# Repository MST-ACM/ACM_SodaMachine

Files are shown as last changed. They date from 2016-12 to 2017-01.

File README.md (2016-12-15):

# ACM Soda Machine Documentation
This documentation details all of information necessary to start, develop, maintain, and update the Soda Machine in CS 213.

## Dependencies
1. [Pyserial](https://github.com/pyserial/pyserial)
  + ```Pyserial``` handles the serial communication of authorization and logging characters between the Raspberry Pi and Arduino platforms in the soda machine.
2. [Pymysql](https://github.com/PyMySQL/PyMySQL)
  + ```Pymsql``` handles the connection to the SQL-lite database stored locally on the Raspberry Pi machine which stores the currency (i.e. how much money each user has).
3. [Libusb1](https://github.com/vpelletier/python-libusb1)
  + ```Libusb1``` handles the interfacing between the LCD screen and the Raspberry Pi so that the Raspberry Pi can write messages to the LCD.
4. [Evdev](https://python-evdev.readthedocs.io/en/latest/)
  + ```Evdev``` handles Kernel input interfacing for the magnetic strip reader when a user swipes their card.
5. [Nanpy](https://github.com/nanpy/nanpy)
  + ```Nanpy``` handles the direct throughput and communication to the arduino board through python.

## Installation
When migrating or reinstalling the system, please follow the following commands on the Raspberry Pi shell to install the main soda machine files ```NOT DEPENDENCIES```:
```
mkdir ~/pi/Soda-Machine/
cd ~/pi/Soda-Machine/
git init
git clone https://github.com/MST-ACM/ACM_SodaMachine_2.0.git
chmod +x main.py bin/smadmin bin/smdaemon
mv Documentation/sodamachine.init /etc/init.d/sodamachine
sudo update-rc.d sodamachine defaults
sudo service sodamachine restart
```
## Pseudocode Overview
1. The user swipes their Student ID into the magnetic strip reader which the magnetic strip reader translates to a ```Student ID```
2. ```Main.py``` performs a database lookup on the Student ID to determine if the user has the required funds.
3. If the database lookup is successful, the Raspberry Pi sends an authorization character to the Arduino using the serial connection.
  - If the database lookup is not successful the transaction fails and the Raspberry Pi resets it transaction state.
4. After the Arduino receives the authorization character, it waits for the user to press a button on the soda machine
  - If the user does not press a button after a certain amount of seconds, the transaction fails and the Raspberry Pi and Arduino reset their states.
5. After the user presses a button, the Arduino turns on the motor associated with the button until the soda is dispensed.
6. After the soda is dispensed, the Arduino sends a success character back to the Raspberry Pi so that the Raspberry Pi charges the user for the soda
  - The user is charged here instead of step 4 to prevent any errors with a soda failing to be dispensed.
7. Then, the Arduino and Raspberry Pi reset their states for the next transaction.

## Contribute
Please contact [acm@mst.edu](acm@mst.edu) if you would like to contribute to this project.

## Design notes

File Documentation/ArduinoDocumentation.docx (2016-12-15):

Arduino Mega code is a slightly modified C code. A reference page can be found at the following website, showing Arduino specific functions and their uses: http://arduino.cc/en/Reference/HomePage. The Arduino Mega code is is broken into two main pieces. The first peice of code is simply initialization of the Arduino Mega and the pins it will be accessing. It also runs through each of the motors and rotates them to a proper starting position and checks the stock to set empty as appropriate.

The second bit of code is the main loop. This loop will just continually cycle while the machine is running. The loop itself is broken into two sub-loops.

The first sub-loop waits for proper authorization to be given by the Raspberry Pi. Presumably a card swipe will be used by the Raspberry Pi to give authorization, though any authorization methods would work. All authorization checks should be done here. Currently, the code automatically authorizes a user. This is for testing purposes only.

The second sub-loop continuously cycles a for-loop waiting for button-press input corresponding to a still stocked soda. At this point the controller will power a motor, have it remained powered until it completes its cycle appropriately then end powering a motor while revoking purchasing permission. Currently, the code does not revoke permission, simply leaving it as “true”. If soda stock is low, the The sub-loop will end and return to the first sub-loop, waiting for authorization again.

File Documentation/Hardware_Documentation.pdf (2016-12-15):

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

ACM Soda Machine

## Introduction

In this document, the reader will nd information on the theory of operation and design of the ACM Soda Machine. Aspects of the soda machine that will be discussed in detail include the controller and the overall wiring of the machine. After reading this document, the reader will have an understanding of how the controller interfaces with machine components such as buttons and motors.

## Overview

A block diagram representation of the overall system can be seen in Figure 1.

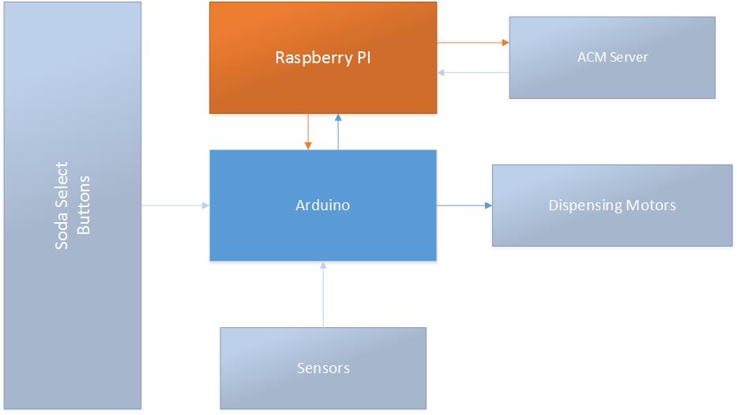
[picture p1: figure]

Figure 1: System Block Diagram

The controller is represented by the block labeled Arduino. The controller implements an Arduino Mega 2560 to read inputs as well as to control the motors. Furthermore, it communicates with the Raspberry Pi in order to receive authorization as well as to relay information concerning soda stock. This document will begin by explaining the theory behind motor operation and control, continue to discuss the inventory sensors and soda select buttons, and conclude with a discussion of the controller itself. The discussion on motor operation and soda select buttons must be read with the Arduino environment in mind; in particular, it is recommend that the reader be familiar with the basics of the Arduino (in particular, the important concept is the idea of using digital pins to read inputs as well as to control outputs).
The overall process of dispensing a soda in terms of conrmations, error checking, and general protocol (conrming payment, receiving authorization from the Raspberry Pi, waiting for a button press. . . ) will not be discussed in this document; rather, the operation of each sub-system will be discussed from a hardware perspective.
Throughout this document, signals may be referred to by their signal names; these names correspond to the names that are used in the Eagle Cad design les for the controller.

Hardware Documentation - Page 2 of 13

## Motor Operation

The soda machine has eight motors (Figure 2), each with identical modes of operation. All eight motors require 120 V AC in order to turn on; when a give motor is running, it will draw 1.15 A. Any design modication must take these parameters into consideration. Because of the way that the software is written, it should not be possible for more than one motor to be active at a given time.

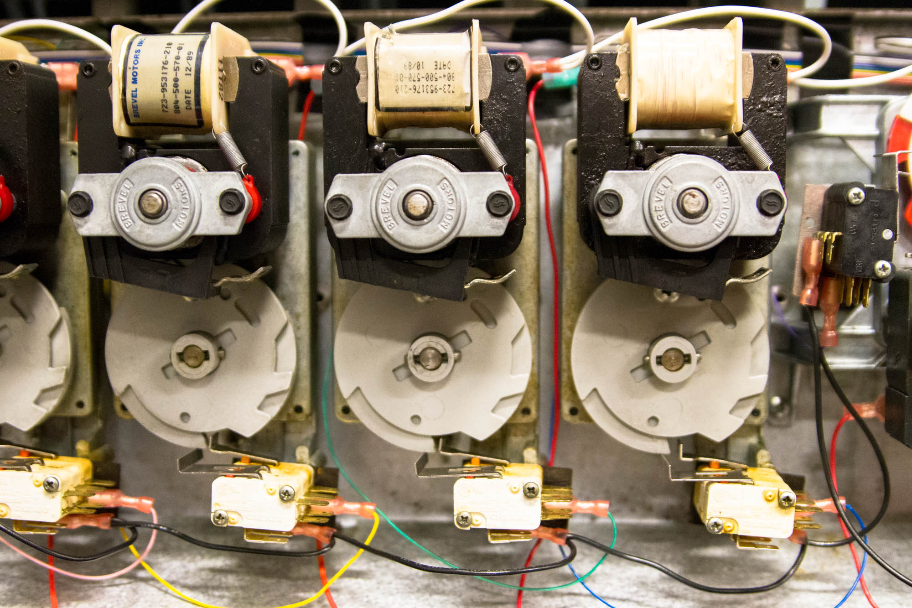
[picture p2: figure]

Figure 2: Machine Motors

The red wires that connect to the left end of the coil windings are connected to the controller; when a motor is to be activated, it is through the red wire that the controller will supply the 120 V AC. All of the motors are tethered to each other via the white wire. The white wire connects directly to the controller, where it is then connected to the neutral line of the 120 V AC power from the socket.
The motor control works by implementing the rotational disks and the switches that are on the motors (Figure 3).

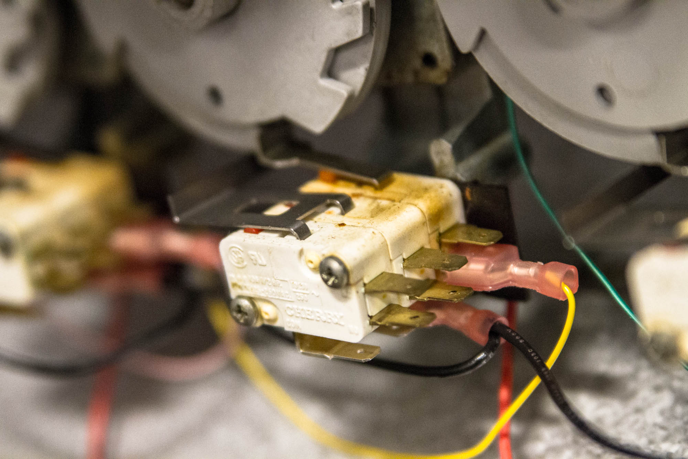
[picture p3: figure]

Figure 3: Motor Control Switch

When a soda is to be dispensed, 120 V AC must be supplied to the appropriate motor for a period of time that is long enough to allow the disk to make a full revolution. In order to achieve the appropriate amount of time, the controller monitors the state of the switch as the motor rotates. When a motor is initially turned on, the controller waits for a short period of time (just enough time for the disk to rotate to a degree where the disk closes the switch) and then it begins monitoring the state of the switch; once the disk makes a full revolution, and when the switch snaps back open, the controller ceases to supply power to the motor.
The black wires that connect each of the switches together are signal ground of the controller. The colored ribbon cable wire of each switch connects to a specic pin on the Arduino through the controller; the pins are held HIGH via internal pull-up resistors in the Arduino. When a motor is mid-rotation and the switch is closed, the ribbon cable wire will short to ground and the controller will supply power for as long as it reads a signal ground from the switch.
The motor numbering convention is 1-8, going from left right, facing the machine. A summary of the wire colors and signal names for the motor system is given in Table 1; a summary of the control signal (ribbon cable wires) mapping to the Arduino's digital pins is given in Table 2. Details concerning the method by which power is supplied to the motors will be provided in the section on the controller itself.
Motor Sub-system | Wire Color | Signal Name
Power | Red | MOTOR1. . . MOTOR8
Power | White | NEUTRAL
Control | Assorted (Ribbon Cable) | CYCLE_SENSE1. . . CYCLE_SENSE8
Control | Black | GND

Table 1: Motor System Wiring

Signal Name | Arduino Pin Number
CYCLE_SENSE1 | 41
CYCLE_SENSE2 | 40
CYCLE_SENSE3 | 39
CYCLE_SENSE4 | 38
CYCLE_SENSE5 | 37
CYCLE_SENSE6 | 36
CYCLE_SENSE7 | 35
CYCLE_SENSE8 | 34

Table 2: Control Signal Pin-mapping

## Inventory Sensors

As the soda cans sit in their slots, they press down on one side of a lever, causing the opposite side to elevate; the opposite side of the lever is the side that presses (or depresses when there is no soda) a mechanical switch. These mechanical switches are the inventory sensors (Figure 4).
Each sensor has two sets of switches that are adjacent to each other: Orienting the switch such that the metal tabs are facing you, the set of tabs on the right-hand side correspond to the inventory stock; the ribbon cable connected to the right-hand side switch connects to pins on the Arduino through the controller.
The inventory switches essentially operate the same way that the motor control switches operate: One end of each inventory switch is connected to the controller's ground and the other end of the switch is connected to a specic pin on the Arduino; the Arduino pin is held HIGH with an internal pull-up resistor and, when a particular soda runs out, the switch is closed and the signal shorts to ground.

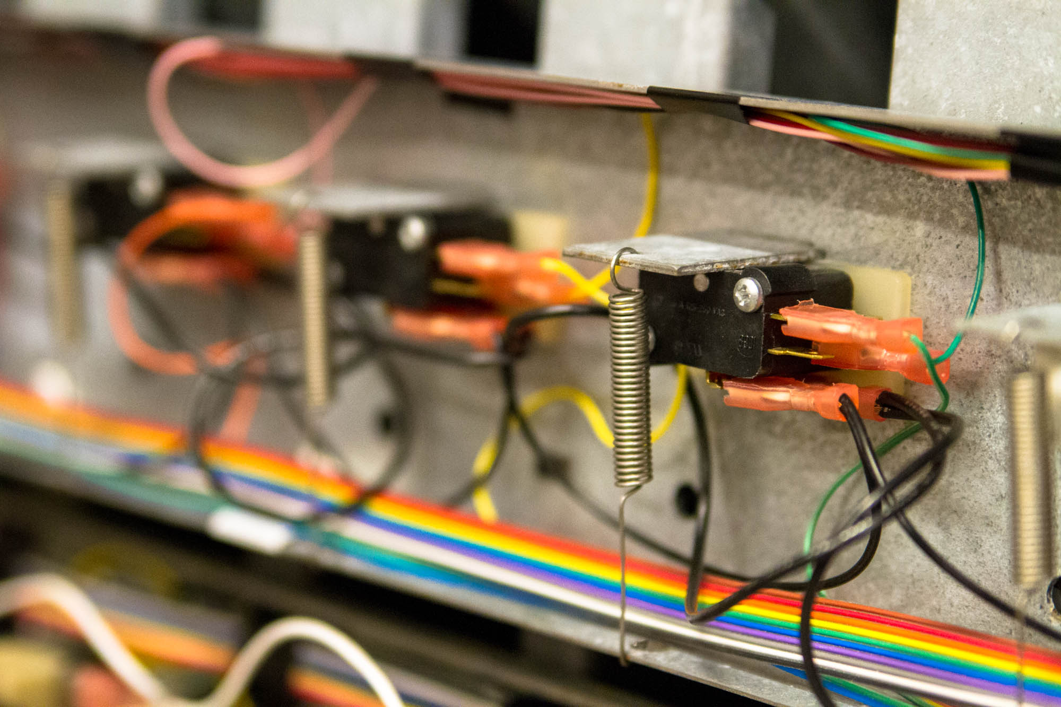
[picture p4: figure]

Figure 4: Inventory Sensors

The Arduino pins used for the stock sensors are analogue pins, as opposed to digital pins (for the purposes of this project, there is little bearing on whether a pin is digital or analogue). The numbering convention of the inventory sensors is identical the motor numbering convention: From left to right, they are 1-8. Table 3 summarizes the inventory signals and their corresponding Arduino pin numbers.

Signal Name | Arduino Pin Number
SENSOR1 | A0
SENSOR2 | A1
SENSOR3 | A2
SENSOR4 | A3
SENSOR5 | A4
SENSOR6 | A5
SENSOR7 | A6
SENSOR8 | A7

Table 3: Inventory Sensor Pin-mapping

The set of tabs on the left-hand side of the inventory switch corresponds to the LEDs of the buttons; these signals do not correspond to any pins on the Arduino. Each LED switch has one end connected to the controller's +5 V pin and the other end of the switch is connected to a particular LED's anode; the cathode of each LED is connected to the controller's ground. When a soda is in stock, the LED will be supplied with power; however, when a particular soda runs out and the lever presses down on the switch, the LED will be disconnected from the power supply and the LED will turn o.

NOTE: At it its current state, there is a set of wires, one green (which connects to ground) and one blue (which connects to +5 V ), running from the LED switches to the controller. At the controller end, the wires have pins on their ends, but they are not plugged into the connector that would mate with the +5 V /GND headers on the controller. DO NOT neglect obtaining the proper connector before connecting the wires to the board; if you do, you risk shorting the +5 V pin on the Arduino with the GND pin, which could cause the Arduino to fry if it goes unnoticed. The appropriate connector that is needed for this is a Molex connector (MFG Part#: 22-01-2025). It might be possible to obtain free samples of this connector directly from Molex; if not, they are available on Mouser.

## Soda Select Buttons

The soda select buttons (Figure 5) essentially operate the same way that the motor control and inventory switches operate: One end of each button is connected to the controller's ground and the other end of the button is connected to a specic pin on the Arduino; the Arduino pin is held HIGH with an internal pull-up resistor and, when a button is pressed, the Arduino recognizes the short to ground.

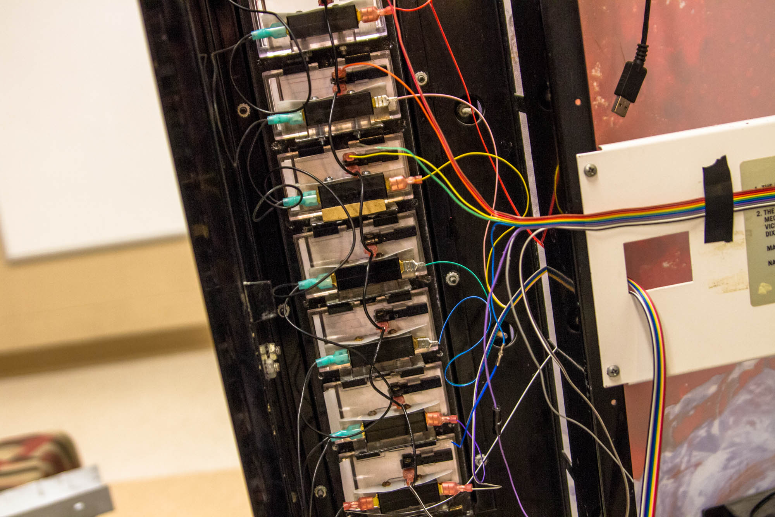
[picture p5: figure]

Figure 5: Soda Select Buttons

The ribbon cable labeled as Buttons is the one that corresponds to the Arduino pins involved with monitoring the button select system; the Arduino pins used for the buttons are analogue pins, as opposed to digital pins. The button numbering convention is 1-8, going from top to bottom. Table 4 summarizes the button signals and their corresponding Arduino pin numbers.

Signal Name | Arduino Pin Number
BUTTON1 | A8
BUTTON2 | A9
BUTTON3 | A10
BUTTON4 | A11
BUTTON5 | A12
BUTTON6 | A13
BUTTON7 | A14
BUTTON8 | A15

Table 4: Soda Select Button Pin-mapping

## The Controller

The controller can be seen in Figure 6.

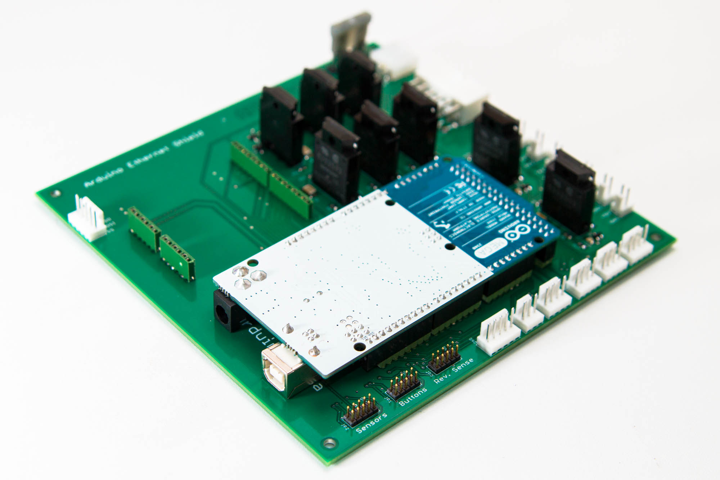
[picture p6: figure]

Figure 6: The Controller

Power Connector

The power connector can be seen in Figure 7.

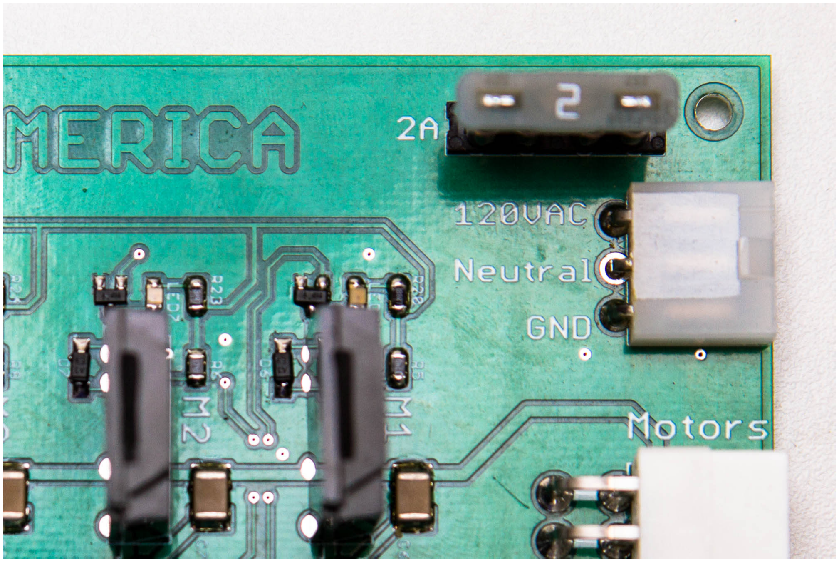
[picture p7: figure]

Figure 7: Power Connector

The Neutral line goes immediately to a pin on the adjacent Motors connector, from where it goes to the motors. At its current state, the GND line goes directly to a pin on the Motors connector, but to nowhere else; in the future, a wire could be run from this GND pin and connect to the machine chassis via a round terminal. The 120 V AC line is distributed to one of the output pins of each motor relay (Figure has the 120 V AC signal highlighted).

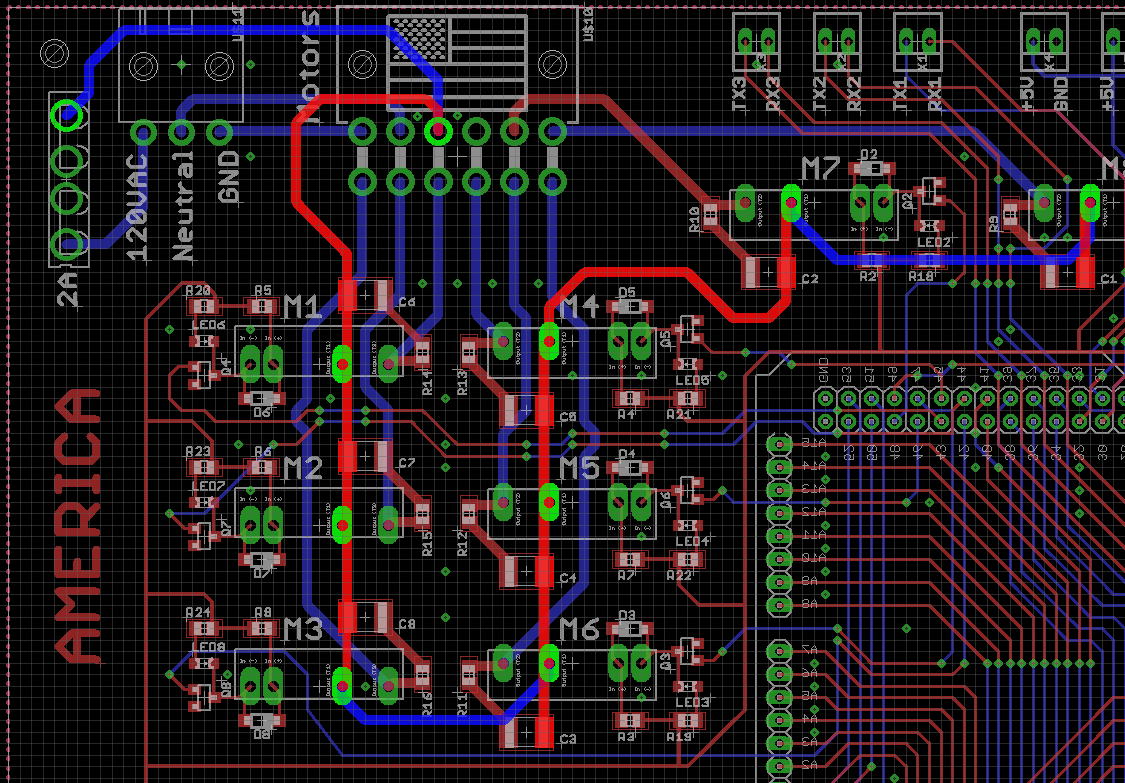
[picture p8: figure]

Figure 8: 120 V AC Highlighted

However, before the 120 V AC line is distributed, it goes through a fuse; the fuse protects the board from current surges. The 120 V AC traces have widths of 40 mils; using a copper thickness of 1 oz/f t² ,
the current carrying capability of the traces is about 2.4 A. The fuse must be able to carry more than 1.15 A, but MUST NOT BE ABLE TO CARRY MORE THAN 2.4 A. A 2.0 A fuse is recommended. The fuse holder takes ATC blade fuses.
The second output pin of each relay is connected to a pin on the Motors connector; these pins are what connect to the motors through the red wires.

Motors Connector

The numbering convention for the pins on the Motors connector follows what is indicated in Figure 9. Table 5 gives the signal names corresponding to the pins on the Motors connector.

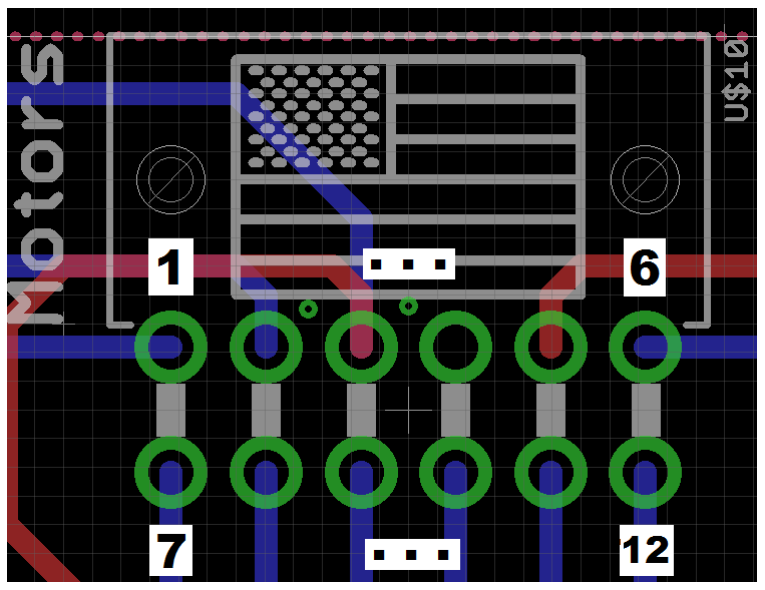
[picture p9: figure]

Figure 9: Motor Connector Numbering

Connector Pin Number | Signal Name
1 | 120VAC-GND
2 | NEUTRAL
3 | 120VAC
4 | NC
5 | MOTOR7
6 | MOTOR8
7 | MOTOR3
8 | MOTOR2
9 | MOTOR1
10 | MOTOR4
11 | MOTOR5
12 | MOTOR6

Table 5: Motors Connector Pin-out

Relay Circuitry

The relays that are used to interface between the Arduino and the motors are solid state relays made by Sharp Microelectronics (MFG Part #: S202S01F). Between the input and output sides, the relays provide 4.0 kV of isolation and they are rated for 8.0 A. The relay circuitry for a single motor is shown in Figure 10.

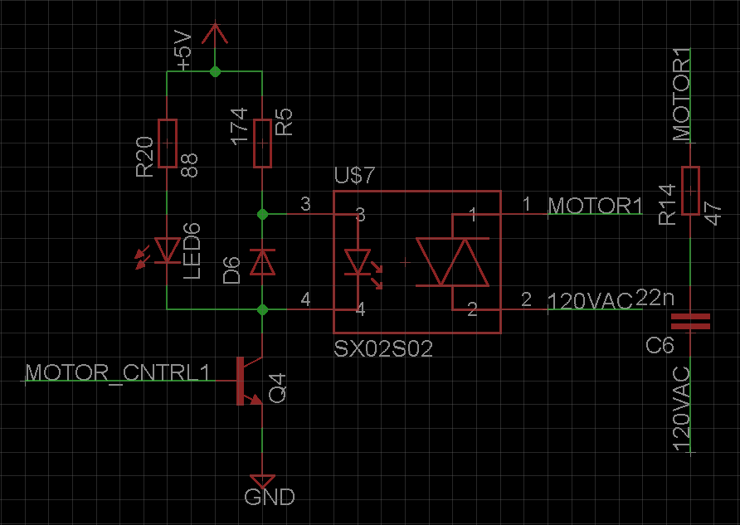
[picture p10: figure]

Figure 10: Relay Circuitry

Essentially, in order to turn a motor on, the internal LED of the relay needs to be turned on. This is accomplished by rst supplying +5 V to the anode pin of the relay while also using a current-limiting resistor to protect the internal LED. The signal, MOTOR_CNTRL1, connects to a digital pin on the Arduino. When this signal goes HIGH, the transistor turns on, completing the input circuit of the relay and allowing current to ow through the relay LED. When this happens, MOTOR1 (which connects to the rst motor through the Motors connector) is connected to the 120 V AC line, turning the motor on. The motor control signal (in this case, MOTOR_CNTRL1) remains HIGH until the motor makes a full revolution; that is, it remains HIGH until the Arduino ceases to read a LOW state from the motor control signal (in this case, the rst motor would remain on until CYCLE_SENSE1 stopped registering as LOW). When a motor is to be turned o, the motor control signal is set to LOW, essentially creating an open-circuit condition in the relay's input circuit.
Table 6 summarizes the motor control signals and their corresponding Arduino pin numbers.
Signal Name | Arduino Pin Number
MOTOR_CNTRL1 | 44
MOTOR_CNTRL2 | 43
MOTOR_CNTRL3 | 42
MOTOR_CNTRL4 | 45
MOTOR_CNTRL5 | 46
MOTOR_CNTRL6 | 47
MOTOR_CNTRL7 | 48
MOTOR_CNTRL8 | 49

Table 6: Motor Control Pin-mapping

Communication and Auxiliary Pins

The controller has easy access to the Arduino's communication pins; the communication pins are summarized in Table 7.

Signal Name | Arduino Pin Number
MISO | 50
MOSI | 51
SCK | 52
SS | 53
TX3 | 14
RX3 | 15
TX2 | 16
RX2 | 17
TX1 | 18
RX1 | 19

Table 7: Communication Pin-mapping

Furthermore, the controller has six auxiliary ports that provide easy access to all other unused Arduino pins. Table 8 gives the Arduino pin numbers corresponding to each auxiliary pin.

Auxiliary Port 1

Signal Name | Pin Number
AUX1.1 | 31
AUX1.2 | 32
AUX1.3 | 33

Auxiliary Port 2

Signal Name | Pin Number
AUX2.1 | 28
AUX2.2 | 29
AUX2.3 | 30

Auxiliary Port 3

Signal Name | Pin Number
AUX3.1 | 25
AUX3.2 | 26
AUX3.3 | 27

Auxiliary Port 4

Signal Name | Pin Number
AUX4.1 | 22
AUX4.2 | 23
AUX4.3 | 24 | AUX6.3 | 12
| | AUX6.4 | 13

Auxiliary Port 5

Signal Name | Pin Number
AUX5.1 | 21
AUX5.2 | 20

Auxiliary Port 6

Signal Name | Pin Number
AUX6.1 | 10
AUX6.2 | 11

Table 8: Pin-mapping for Auxiliary Ports

Establishing Communication With the Raspberry Pi

Perhaps the simplest way to establish communication between the Raspberry Pi and the Arduino would be to take advantage of the Arduino's I

2C pins, which can easily be accessed with auxiliary

pins AUX5.1 (SCL) and AUX5.2 (SDA).

NOTE: DO NOT use this method unless the Raspberry Pi is being run as a master and the Arduino is being run as a slave. If the situation is otherwise, you will need to use a dierent method that incorporates a logic level converter to interface between the Raspberry Pi and the Arduino.

The header which has AUX5.1 and AUX5.2 is a three-pin header which also includes GND. In order to connect with the Raspberry Pi, simply connect the Arduino's GND to the Raspberry Pi's GND, AUX5.1 with the Pi's SCL pin, and AUX5.2 with the Pi's SDA pin.

For cable assembly: The wires on the Arduino end of the cable will need to be tted with crimp terminals (Molex Part #: 39-00-0039) which will be fed into a mating connector (Molex Part #: 22-01-2035). Be sure to orient the wires into the connector correctly so that the pins on the Arduino connect to the correct pins on the Raspberry Pi.

Further details can be found here: http://blog.oscarliang.net/raspberry-pi-arduino-connected-i2c/.

## Final Notes

During the nal testing of the controller, it was noticed that if the machine is turned o and then turned back on too quickly, there is a possibility of blowing the fuse. For this reason, it is recommended that, when the machine is turned o, it be given a chance to cool down for about 10 seconds before turning it back on.
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

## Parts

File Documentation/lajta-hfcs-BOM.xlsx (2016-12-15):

Board Name: | lajta-hfcs | Quantity: | 2
Description: | Controller for ACM soda machine.
Board Vrsn: | 1V1 | Client: | ACM
Date: | 2014-05-14
Item # | Qty | Totals | Ref Des | Value | Manufacturer | Mfg Part # | Digikey Part # | Mouser Part # | Description | Package | Alt Mfg Part #s
PCB Assembly
1 | 8 | 16 | C1, C2, C3, C4, C5, C6, C7, C8 | 22n | Murata | GA243QR7E2223MW01L |  | 81-GA243QR7E2223MW1L (http://www.mouser.com/ProductDetail/Murata-Electronics/GA243QR7E2223MW01L/) | Multilayer Ceramic Capacitors MLCC - SMD/SMT .022uF 250Volts 20% | C1812
2 | 8 | 16 | D1, D2, D3, D4, D5, D6, D7, D8 | 1N4448W | Vishay | 1N4448W-E3-08 |  | 78-1N4448W-E3-08 (http://www.mouser.com/ProductDetail/Vishay-Semiconductors/1N4448W-E3-08/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) | Diodes - General Purpose, Power, Switching 100 Volt 500mA 4ns | SOD123
3 | 1 | 2 | IC1-SNGL-HDR |  | TE | 5-826629-0 |  | 571-5-826629-0 (http://www.mouser.com/ProductDetail/TE-Connectivity-AMP/5-826629-0/) | Headers & Wire Housings 50P SINGLE ROW | HDR
4 | 2 | 4 | IC1-DBL-HDR |  | Molex | 10-89-7361 |  | 538-10-89-7361 (http://www.mouser.com/ProductDetail/Molex/10-89-7361/) | Headers & Wire Housings 2.54MM HDR VT 2X18P 240/110 SNPB | HDR
5 | 3 | 6 | JP1, JP2, JP3 |  | 3M | 951210-8622-AR |  | 517-951210-8622-AR (http://www.mouser.com/ProductDetail/3M-Electronic-Solutions-Division/951210-8622-AR/) | Headers & Wire Housings 10P PIN STRP HDR 2R STRT PTH 10U AU | 2X05M
6 | 8 | 16 | LED1, LED2, LED3, LED4, LED5, LED6, LED7, LED8 |  | OSRAM Opto | LS R976-NR-1 |  | 720-LSR976-NR-1 (http://www.mouser.com/ProductDetail/OSRAM-Opto-Semiconductors/LS-R976-NR-1/) | Standard LEDs - SMD Super Red, 633nm 180mcd, 20mA | CHIPLED_0805
7 | 8 | 16 | Q1, Q2, Q3, Q4, Q5, Q6, Q7, Q8 | MMBT2222A | Fairchild | MMBT2222A |  | 512-MMBT2222A (http://www.mouser.com/ProductDetail/Fairchild-Semiconductor/MMBT2222A/) | Transistors Bipolar - BJT SOT-23 NPN GEN PUR | SOT23
8 | 8 | 16 | R1, R2, R3, R4, R5, R6, R7, R8 | 174 | Vishay | CRCW0805174RFKEA |  | 71-CRCW0805-174-E3 (http://www.mouser.com/ProductDetail/Vishay-Dale/CRCW0805174RFKEA/) | Thick Film Resistors - SMD 1/8watt 174ohms 1% 100ppm | R0805
9 | 8 | 16 | R9, R10, R11, R12, R13, R14, R15, R16 | 47 | Vishay | CRCW080547R0FKEB |  | 71-CRCW080547R0FKEB (http://www.mouser.com/ProductDetail/Vishay-Dale/CRCW080547R0FKEB/) | Thick Film Resistors - SMD 1/8watt 47ohms 1% | R0805
10 | 8 | 16 | R17, R18, R19, R20, R21, R22, R23, R24 | 88 | Vishay | CRCW080588R7FKEA |  | 71-CRCW0805-88.7-E3 (http://www.mouser.com/ProductDetail/Vishay/CRCW080588R7FKEA/) | Thick Film Resistors - SMD 1/8watt 88.7ohms 1% 100ppm | R0805
11 | 2 | 4 | U$1 | 1x8 | TE | 215297-8 |  | 571-215297-8 (http://www.mouser.com/ProductDetail/TE-Connectivity-AMP/215297-8/) | Headers & Wire Housings 8P HV-100 FED-LEI | ETHERNET_SHIELD
12 | 2 | 4 | U$1 | 1x6 | TE | 215299-6 |  | 571-215299-6 (http://www.mouser.com/ProductDetail/TE-Connectivity-AMP/215299-6/) | Headers & Wire Housings 6P RECPT VERT HV-100
13 | 8 | 16 | U$2, U$3, U$4, U$5, U$6, U$7, U$8, U$9 | SX02S02 | Sharp | S202S01F |  | 852-S202S01F (http://www.mouser.com/ProductDetail/Sharp-Microelectronics/S202S01F/) | Solid State Relays - PCB Mount 4-SIP NON-ZC 8mA | SIP-4
14 | 1 | 2 | U$10 | 39-30-0120 | Molex | 39-30-0120 |  | 538-39-30-0120 (http://www.mouser.com/ProductDetail/Molex/39-30-0120/) | Headers & Wire Housings 12 CKT R/A HEADER | MINIFIT5569-2-6
15 | 1 | 2 | U$11 | 39-30-3035 | Molex | 39-30-3035 |  | 538-39-30-3035 (http://www.mouser.com/ProductDetail/Molex/39-30-3035/) | Headers & Wire Housings 3 CKT R/A HEADER
16 | 1 | 2 | U$12 | 3522 | Keystone | 3522-2 |  | 534-3522-2 (http://www.mouser.com/ProductDetail/Keystone-Electronics/3522-2/) | Fuse Holder AUTO FUSEHOLDER .025 | 3522-2
17 | 6 | 12 | X1, X2, X3, X4, X5, X12 | 22-23-2021 | Molex | 22-23-2021 |  | 538-22-23-2021 (http://www.mouser.com/ProductDetail/Molex/39-01-2120/) | Headers & Wire Housings VERT PCB HDR 2P TIN FRICTION LOCK | 22-23-2021
18 | 4 | 8 | X6, X7, X8, X9 | 22-23-2041 | Molex | 22-23-2041 |  | 538-22-23-2041 (http://www.mouser.com/ProductDetail/Keystone-Electronics/3522-2/) | Headers & Wire Housings VERT PCB HDR 4P TIN FRICTION LOCK | 22-23-2041
19 | 1 | 2 | X11 | 22-23-2031 | Molex | 22-23-2031 |  | 538-22-23-2031 (http://www.mouser.com/ProductDetail/Cooper-Bussmann/BK-ATC-2/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) | Headers & Wire Housings VERT PCB HDR 3P TIN FRICTION LOCK | 22-23-2031
20 | 2 | 4 | X10, X13 | 22-23-2051 | Molex | 22-23-2051 |  | 538-22-23-2051 | Headers & Wire Housings VERT PCB HDR 5P TIN FRICTION LOCK | 22-23-2051
Additional Parts (Mating connectors, fuse, crimp terminals, etc.)
21 | 1 | 2 | U$12 (Fuse) | 2A 32V | Cooper | BK/ATC-2 |  | 504-BK/ATC-2 (http://www.mouser.com/ProductDetail/Cooper-Bussmann/BK-ATC-2/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) | Automotive Fuses BUSS ATC FUSE | ATC
22 | 1 | 2 | U$11-Cable-End (Power Connector) | 39-01-4031 | Molex | 39-01-4031 |  | 538-39-01-4031 (http://www.mouser.com/ProductDetail/Molex/39-01-4031/) | Headers & Wire Housings 3 CKT RCPT HOUSING
23 | 1 | 2 | U$10-Mating-End (Motor Connector) | 39-01-2120 | Molex | 39-01-2120 |  | 538-39-01-2120 (http://www.mouser.com/ProductDetail/Molex/39-01-2120/) | Headers & Wire Housings 12 CKT RCPT HOUSING
24 | 15 | 30 | U$10-Crimp-Terminals | 39-00-0039 | Molex | 39-00-0039 |  | 538-39-00-0039 (http://www.mouser.com/ProductDetail/Molex/39-00-0039/) | Headers & Wire Housings SOCKET 24-18AWG BULK
25 | 3 | 6 | Ribbon-Cable-Female-Connector | 1-111623-8 | TE | 1-111623-8 |  | 571-1-111623-8 (http://www.mouser.com/ProductDetail/TE-Connectivity/1-111623-8/) | Headers & Wire Housings 2MM REC 2X05P POL FEED THRU
26 | 1 | 2 | Arduino Mega | Mega | Arduino | A000067 |  | 782-A000067 (http://www.mouser.com/ProductDetail/Arduino/A000067/) | Development Boards & Kits - AVR ARDUINO MEGA2560 REV 3
27 | 1 | 2 | Arduino Ethernet Shield | Ethernet Shield | Arduino | A000072 |  | 782-A000072 (http://www.mouser.com/ProductDetail/Arduino/A000072/) | Ethernet Development Tools ARDUINO ETHERNET SHD MIC-SD W/O PoE REV 3
28 | 6 | 12 | X1, X2, X3, X4, X5, X12 (mating connector) | 22-01-2025 | Molex | 22-01-2025 |  | 538-22-01-2025 (http://www.mouser.com/ProductDetail/Molex/22-01-2025/) | Headers & Wire Housings 2 CRT CRIMP HOUSING | 6471
29 | 4 | 8 | X6, X7, X8, X9 (mating connector) | 22-01-2045 | Molex | 22-01-2045 |  | 538-22-01-2045 (http://www.mouser.com/ProductDetail/Molex/22-01-2045/) | Headers & Wire Housings 4 CRT TERM HOUSING | 6471
30 | 1 | 2 | X11 (mating connector) | 22-01-2035 | Molex | 22-01-2035 |  | 538-22-01-2035 (http://www.mouser.com/ProductDetail/Molex/22-01-2035/) | Headers & Wire Housings 3 CRT TERM HOUSING | 6471
31 | 2 | 4 | X10, X13 (mating connector) | 22-01-2055 | Molex | 22-01-2055 |  | 538-22-01-2055 (http://www.mouser.com/ProductDetail/Molex/22-01-2055/) | Headers & Wire Housings 5 CRT TERM HOUSING | 6471

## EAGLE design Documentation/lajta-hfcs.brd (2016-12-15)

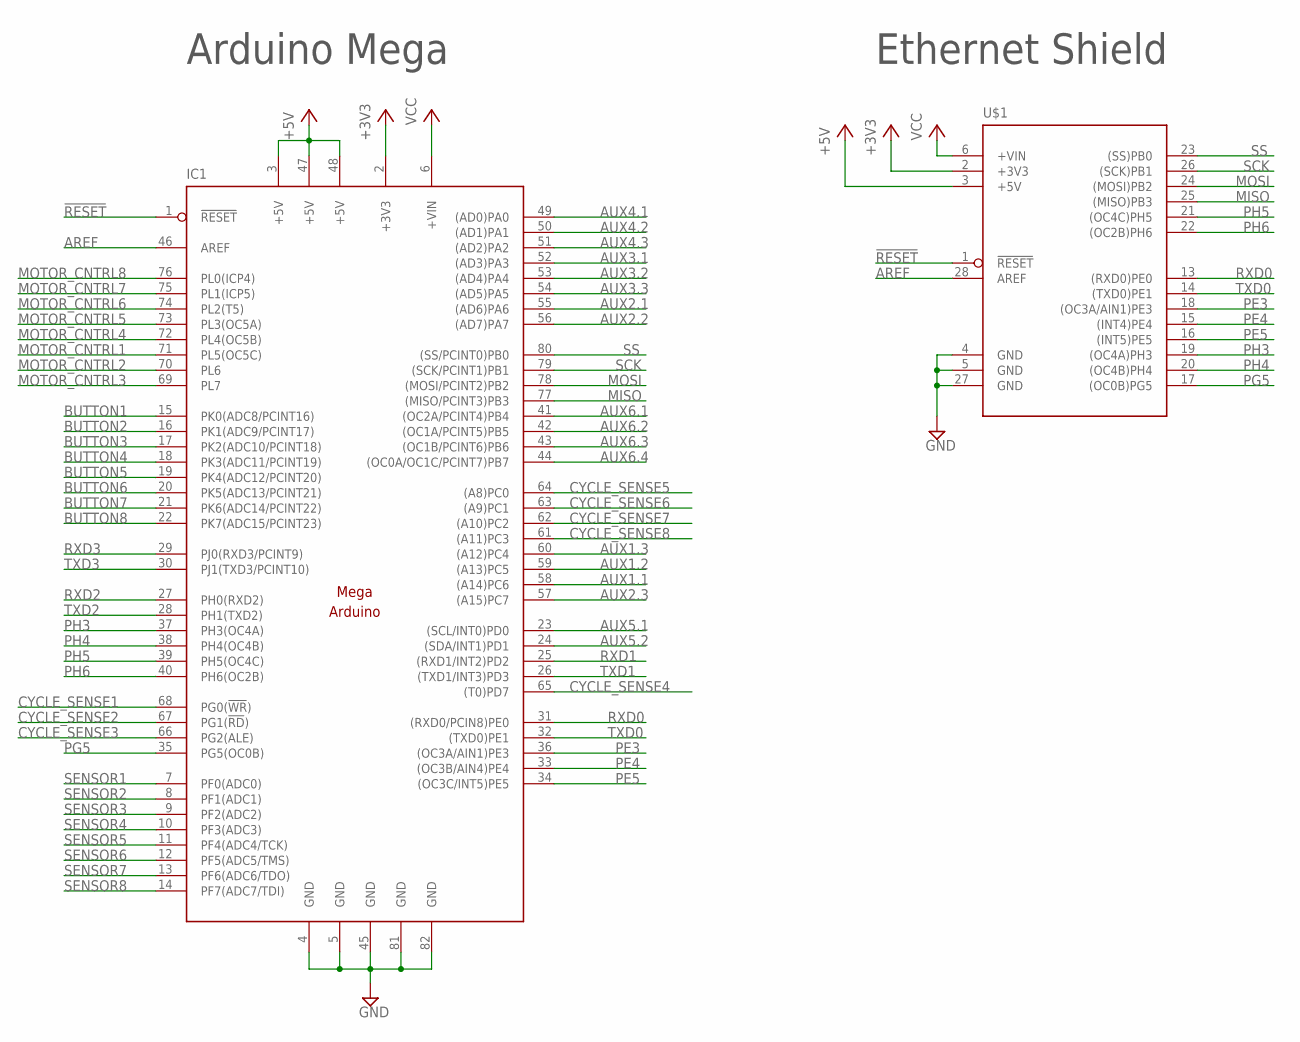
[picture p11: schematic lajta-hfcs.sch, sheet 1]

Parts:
IC1: MEGAARDUINO_1; MEGA_ARDUINO
U$1: MEGAARDUINO_ETHERNET_SHIELD; ETHERNET_SHIELD

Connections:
!RESET: IC1.1 (!RESET), U$1.1 (!RESET)
+3V3: IC1.2 (+3V3), U$1.2 (+3V3)
+5V: IC1.3 (+5V), IC1.47 (+5V), IC1.48 (+5V), U$1.3 (+5V); also elsewhere on the board
AREF: IC1.46 (AREF), U$1.28 (AREF)
AUX1.1: IC1.58 ((A14)PC6); also elsewhere on the board
AUX1.2: IC1.59 ((A13)PC5); also elsewhere on the board
AUX1.3: IC1.60 ((A12)PC4); also elsewhere on the board
AUX2.1: IC1.55 ((AD6)PA6); also elsewhere on the board
AUX2.2: IC1.56 ((AD7)PA7); also elsewhere on the board
AUX2.3: IC1.57 ((A15)PC7); also elsewhere on the board
AUX3.1: IC1.52 ((AD3)PA3); also elsewhere on the board
AUX3.2: IC1.53 ((AD4)PA4); also elsewhere on the board
AUX3.3: IC1.54 ((AD5)PA5); also elsewhere on the board
AUX4.1: IC1.49 ((AD0)PA0); also elsewhere on the board
AUX4.2: IC1.50 ((AD1)PA1); also elsewhere on the board
AUX4.3: IC1.51 ((AD2)PA2); also elsewhere on the board
AUX5.1: IC1.23 ((SCL/INT0)PD0); also elsewhere on the board
AUX5.2: IC1.24 ((SDA/INT1)PD1); also elsewhere on the board
AUX6.1: IC1.41 ((OC2A/PCINT4)PB4); also elsewhere on the board
AUX6.2: IC1.42 ((OC1A/PCINT5)PB5); also elsewhere on the board
AUX6.3: IC1.43 ((OC1B/PCINT6)PB6); also elsewhere on the board
AUX6.4: IC1.44 ((OC0A/OC1C/PCINT7)PB7); also elsewhere on the board
BUTTON1: IC1.15 (PK0(ADC8/PCINT16)); also elsewhere on the board
BUTTON2: IC1.16 (PK1(ADC9/PCINT17)); also elsewhere on the board
BUTTON3: IC1.17 (PK2(ADC10/PCINT18)); also elsewhere on the board
BUTTON4: IC1.18 (PK3(ADC11/PCINT19)); also elsewhere on the board
BUTTON5: IC1.19 (PK4(ADC12/PCINT20)); also elsewhere on the board
BUTTON6: IC1.20 (PK5(ADC13/PCINT21)); also elsewhere on the board
BUTTON7: IC1.21 (PK6(ADC14/PCINT22)); also elsewhere on the board
BUTTON8: IC1.22 (PK7(ADC15/PCINT23)); also elsewhere on the board
CYCLE_SENSE1: IC1.68 (PG0(!WR!)); also elsewhere on the board
CYCLE_SENSE2: IC1.67 (PG1(!RD!)); also elsewhere on the board
CYCLE_SENSE3: IC1.66 (PG2(ALE)); also elsewhere on the board
CYCLE_SENSE4: IC1.65 ((T0)PD7); also elsewhere on the board
CYCLE_SENSE5: IC1.64 ((A8)PC0); also elsewhere on the board
CYCLE_SENSE6: IC1.63 ((A9)PC1); also elsewhere on the board
CYCLE_SENSE7: IC1.62 ((A10)PC2); also elsewhere on the board
CYCLE_SENSE8: IC1.61 ((A11)PC3); also elsewhere on the board
GND: IC1.4 (GND), IC1.5 (GND), IC1.45 (GND), IC1.81 (GND), IC1.82 (GND), U$1.4 (GND), U$1.5 (GND), U$1.27 (GND); also elsewhere on the board
MISO: IC1.77 ((MISO/PCINT3)PB3), U$1.25 ((MISO)PB3); also elsewhere on the board
MOSI: IC1.78 ((MOSI/PCINT2)PB2), U$1.24 ((MOSI)PB2); also elsewhere on the board
MOTOR_CNTRL1: IC1.71 (PL5(OC5C)); also elsewhere on the board
MOTOR_CNTRL2: IC1.70 (PL6); also elsewhere on the board
MOTOR_CNTRL3: IC1.69 (PL7); also elsewhere on the board
MOTOR_CNTRL4: IC1.72 (PL4(OC5B)); also elsewhere on the board
MOTOR_CNTRL5: IC1.73 (PL3(OC5A)); also elsewhere on the board
MOTOR_CNTRL6: IC1.74 (PL2(T5)); also elsewhere on the board
MOTOR_CNTRL7: IC1.75 (PL1(ICP5)); also elsewhere on the board
MOTOR_CNTRL8: IC1.76 (PL0(ICP4)); also elsewhere on the board
PE3: IC1.36 ((OC3A/AIN1)PE3), U$1.18 ((OC3A/AIN1)PE3)
PE4: IC1.33 ((OC3B/AIN4)PE4), U$1.15 ((INT4)PE4)
PE5: IC1.34 ((OC3C/INT5)PE5), U$1.16 ((INT5)PE5)
PG5: IC1.35 (PG5(OC0B)), U$1.17 ((OC0B)PG5)
PH3: IC1.37 (PH3(OC4A)), U$1.19 ((OC4A)PH3)
PH4: IC1.38 (PH4(OC4B)), U$1.20 ((OC4B)PH4)
PH5: IC1.39 (PH5(OC4C)), U$1.21 ((OC4C)PH5)
PH6: IC1.40 (PH6(OC2B)), U$1.22 ((OC2B)PH6)
RXD0: IC1.31 ((RXD0/PCIN8)PE0), U$1.13 ((RXD0)PE0)
RXD1: IC1.25 ((RXD1/INT2)PD2); also elsewhere on the board
RXD2: IC1.27 (PH0(RXD2)); also elsewhere on the board
RXD3: IC1.29 (PJ0(RXD3/PCINT9)); also elsewhere on the board
SCK: IC1.79 ((SCK/PCINT1)PB1), U$1.26 ((SCK)PB1); also elsewhere on the board
SENSOR1: IC1.7 (PF0(ADC0)); also elsewhere on the board
SENSOR2: IC1.8 (PF1(ADC1)); also elsewhere on the board
SENSOR3: IC1.9 (PF2(ADC2)); also elsewhere on the board
SENSOR4: IC1.10 (PF3(ADC3)); also elsewhere on the board
SENSOR5: IC1.11 (PF4(ADC4/TCK)); also elsewhere on the board
SENSOR6: IC1.12 (PF5(ADC5/TMS)); also elsewhere on the board
SENSOR7: IC1.13 (PF6(ADC6/TDO)); also elsewhere on the board
SENSOR8: IC1.14 (PF7(ADC7/TDI)); also elsewhere on the board
SS: IC1.80 ((SS/PCINT0)PB0), U$1.23 ((SS)PB0); also elsewhere on the board
TXD0: IC1.32 ((TXD0)PE1), U$1.14 ((TXD0)PE1)
TXD1: IC1.26 ((TXD1/INT3)PD3); also elsewhere on the board
TXD2: IC1.28 (PH1(TXD2)); also elsewhere on the board
TXD3: IC1.30 (PJ1(TXD3/PCINT10)); also elsewhere on the board
VCC: IC1.6 (+VIN), U$1.6 (+VIN)

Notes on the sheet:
Arduino Mega
Ethernet Shield

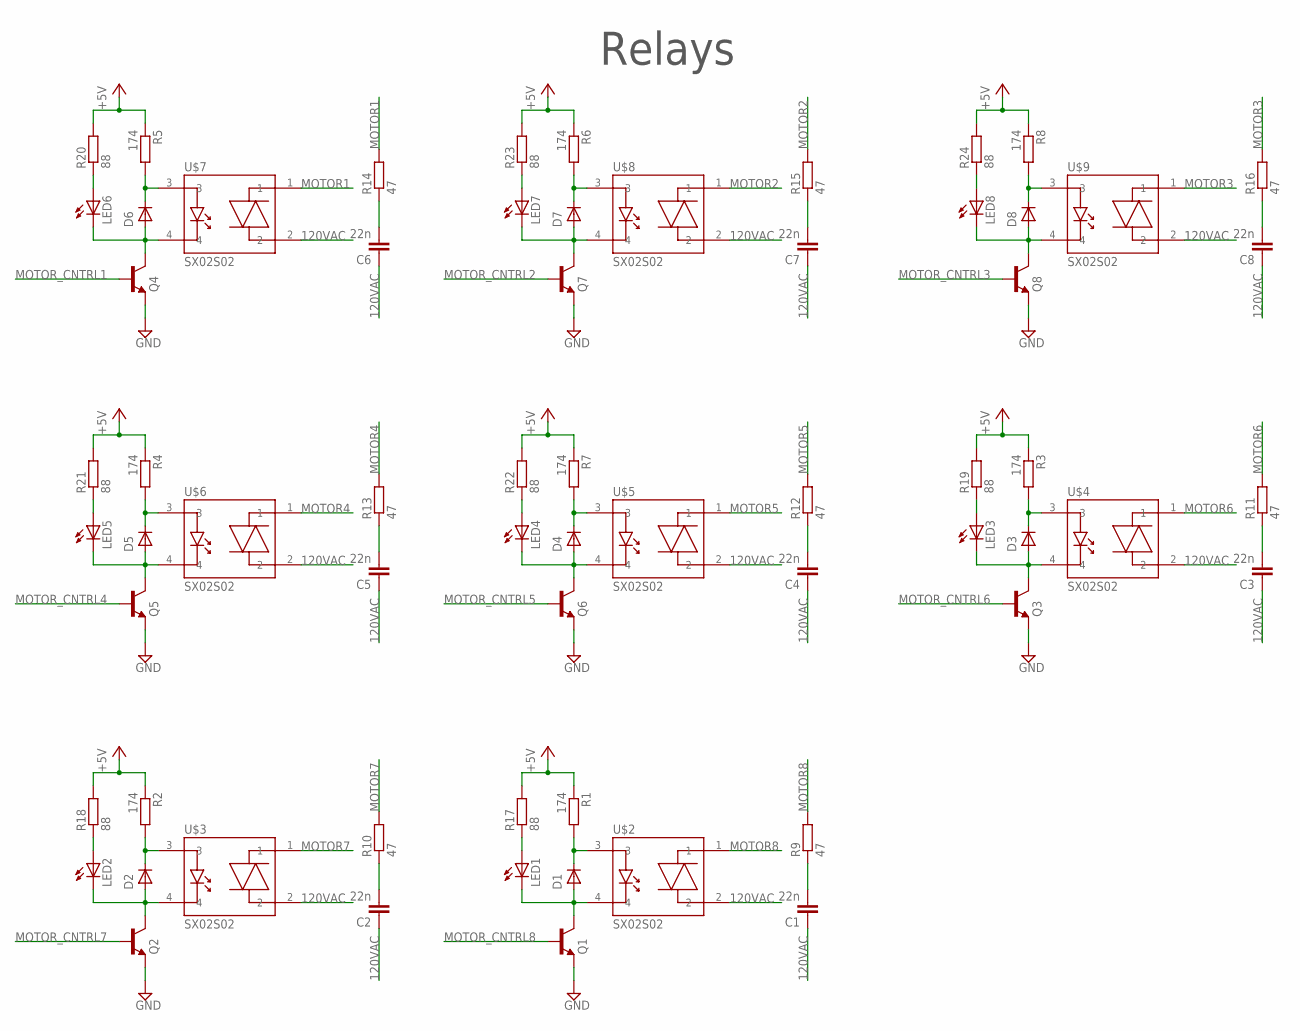
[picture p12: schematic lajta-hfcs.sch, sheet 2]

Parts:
C1, C2, C3, C4, C5, C6, C7, C8: 22n; C1812
D1, D2, D3, D4, D5, D6, D7, D8: 1N4448W; SOD123
LED1, LED2, LED3, LED4, LED5, LED6, LED7, LED8: LEDCHIPLED_0805; CHIPLED_0805
Q1, Q2, Q3, Q4, Q5, Q6, Q7, Q8: MMBT2222A; SOT23
R1, R2, R3, R4, R5, R6, R7, R8: 174; R0805
R9, R10, R11, R12, R13, R14, R15, R16: 47; R0805
R17, R18, R19, R20, R21, R22, R23, R24: 88; R0805
U$2, U$3, U$4, U$5, U$6, U$7, U$8, U$9: SX02S02; SIP-4

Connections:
120VAC: C1.1, C2.1, C3.1, C4.1, C5.1, C6.1, C7.1, C8.1, U$2.2, U$3.2, U$4.2, U$5.2, U$6.2, U$7.2, U$8.2, U$9.2; also elsewhere on the board
+5V: R1.1, R2.1, R3.1, R4.1, R5.1, R6.1, R7.1, R8.1, R17.2, R18.2, R19.2, R20.2, R21.2, R22.2, R23.2, R24.2; also elsewhere on the board
GND: Q1.2 (E), Q2.2 (E), Q3.2 (E), Q4.2 (E), Q5.2 (E), Q6.2 (E), Q7.2 (E), Q8.2 (E); also elsewhere on the board
MOTOR1: R14.2, U$7.1; also elsewhere on the board
MOTOR2: R15.2, U$8.1; also elsewhere on the board
MOTOR3: R16.2, U$9.1; also elsewhere on the board
MOTOR4: R13.2, U$6.1; also elsewhere on the board
MOTOR5: R12.2, U$5.1; also elsewhere on the board
MOTOR6: R11.2, U$4.1; also elsewhere on the board
MOTOR7: R10.2, U$3.1; also elsewhere on the board
MOTOR8: R9.2, U$2.1; also elsewhere on the board
MOTOR_CNTRL1: Q4.1 (B); also elsewhere on the board
MOTOR_CNTRL2: Q7.1 (B); also elsewhere on the board
MOTOR_CNTRL3: Q8.1 (B); also elsewhere on the board
MOTOR_CNTRL4: Q5.1 (B); also elsewhere on the board
MOTOR_CNTRL5: Q6.1 (B); also elsewhere on the board
MOTOR_CNTRL6: Q3.1 (B); also elsewhere on the board
MOTOR_CNTRL7: Q2.1 (B); also elsewhere on the board
MOTOR_CNTRL8: Q1.1 (B); also elsewhere on the board
unnamed: D1.C, R1.2, U$2.3
unnamed: D1.A, LED1.C, Q1.3 (C), U$2.4
unnamed: LED1.A, R17.1
unnamed: D2.C, R2.2, U$3.3
unnamed: D2.A, LED2.C, Q2.3 (C), U$3.4
unnamed: LED2.A, R18.1
unnamed: D3.C, R3.2, U$4.3
unnamed: D3.A, LED3.C, Q3.3 (C), U$4.4
unnamed: LED3.A, R19.1
unnamed: D4.C, R7.2, U$5.3
unnamed: D4.A, LED4.C, Q6.3 (C), U$5.4
unnamed: LED4.A, R22.1
unnamed: D5.C, R4.2, U$6.3
unnamed: D5.A, LED5.C, Q5.3 (C), U$6.4
unnamed: LED5.A, R21.1
unnamed: LED6.A, R20.1
unnamed: D6.A, LED6.C, Q4.3 (C), U$7.4
unnamed: D6.C, R5.2, U$7.3
unnamed: LED7.A, R23.1
unnamed: D7.A, LED7.C, Q7.3 (C), U$8.4
unnamed: D7.C, R6.2, U$8.3
unnamed: LED8.A, R24.1
unnamed: D8.A, LED8.C, Q8.3 (C), U$9.4
unnamed: D8.C, R8.2, U$9.3
unnamed: C8.2, R16.1
unnamed: C7.2, R15.1
unnamed: C4.2, R12.1
unnamed: C5.2, R13.1
unnamed: C6.2, R14.1
unnamed: C3.2, R11.1
unnamed: C2.2, R10.1
unnamed: C1.2, R9.1

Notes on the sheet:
Relays

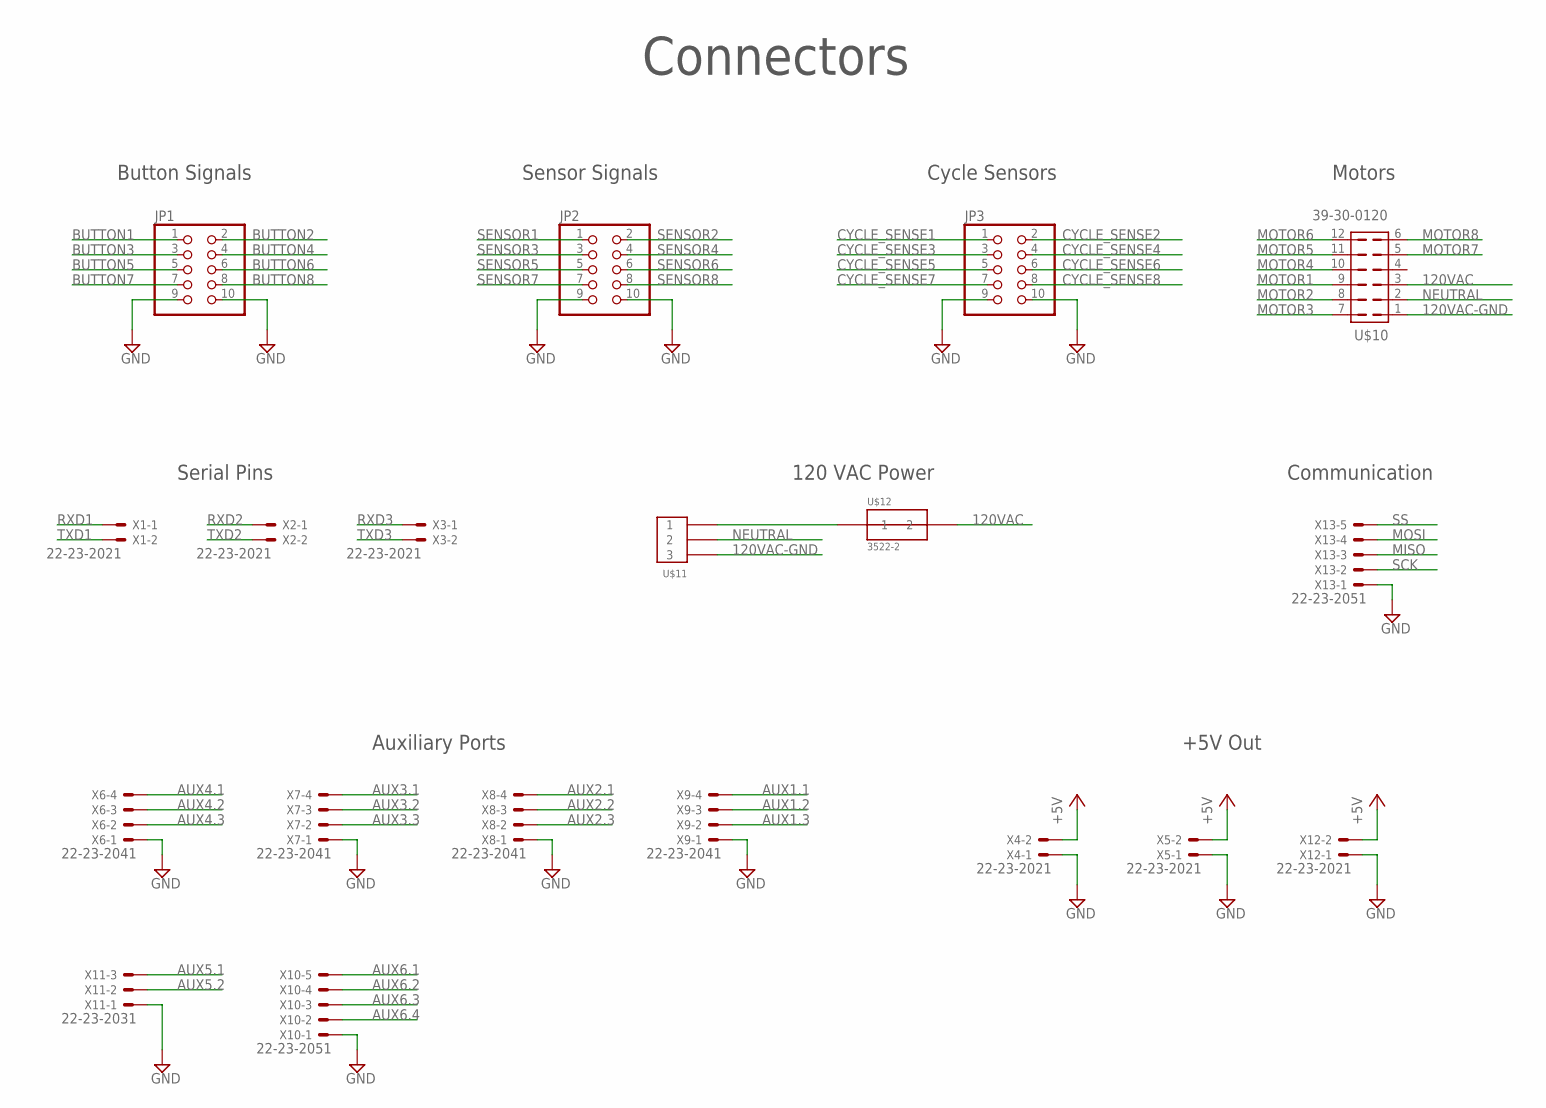
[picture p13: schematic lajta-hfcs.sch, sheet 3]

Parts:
JP1, JP2, JP3: PINHD-2X05_2.00; 2X05M
U$10: 39-30-0120; MINIFIT5569-2-6
U$11: 39-30-3035
U$12: 3522-2; ATC
X1, X2, X3, X4, X5, X12: 22-23-2021
X6, X7, X8, X9: 22-23-2041
X10, X13: 22-23-2051
X11: 22-23-2031

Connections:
120VAC: U$10.3, U$12.4 (2); also elsewhere on the board
120VAC-GND: U$10.1, U$11.3
+5V: X4.2, X5.2, X12.2; also elsewhere on the board
AUX1.1: X9.4; also elsewhere on the board
AUX1.2: X9.3; also elsewhere on the board
AUX1.3: X9.2; also elsewhere on the board
AUX2.1: X8.4; also elsewhere on the board
AUX2.2: X8.3; also elsewhere on the board
AUX2.3: X8.2; also elsewhere on the board
AUX3.1: X7.4; also elsewhere on the board
AUX3.2: X7.3; also elsewhere on the board
AUX3.3: X7.2; also elsewhere on the board
AUX4.1: X6.4; also elsewhere on the board
AUX4.2: X6.3; also elsewhere on the board
AUX4.3: X6.2; also elsewhere on the board
AUX5.1: X11.3; also elsewhere on the board
AUX5.2: X11.2; also elsewhere on the board
AUX6.1: X10.5; also elsewhere on the board
AUX6.2: X10.4; also elsewhere on the board
AUX6.3: X10.3; also elsewhere on the board
AUX6.4: X10.2; also elsewhere on the board
BUTTON1: JP1.1; also elsewhere on the board
BUTTON2: JP1.2; also elsewhere on the board
BUTTON3: JP1.3; also elsewhere on the board
BUTTON4: JP1.4; also elsewhere on the board
BUTTON5: JP1.5; also elsewhere on the board
BUTTON6: JP1.6; also elsewhere on the board
BUTTON7: JP1.7; also elsewhere on the board
BUTTON8: JP1.8; also elsewhere on the board
CYCLE_SENSE1: JP3.1; also elsewhere on the board
CYCLE_SENSE2: JP3.2; also elsewhere on the board
CYCLE_SENSE3: JP3.3; also elsewhere on the board
CYCLE_SENSE4: JP3.4; also elsewhere on the board
CYCLE_SENSE5: JP3.5; also elsewhere on the board
CYCLE_SENSE6: JP3.6; also elsewhere on the board
CYCLE_SENSE7: JP3.7; also elsewhere on the board
CYCLE_SENSE8: JP3.8; also elsewhere on the board
GND: JP1.9, JP1.10, JP2.9, JP2.10, JP3.9, JP3.10, X4.1, X5.1, X6.1, X7.1, X8.1, X9.1, X10.1, X11.1, X12.1, X13.1; also elsewhere on the board
MISO: X13.3; also elsewhere on the board
MOSI: X13.4; also elsewhere on the board
MOTOR1: U$10.9; also elsewhere on the board
MOTOR2: U$10.8; also elsewhere on the board
MOTOR3: U$10.7; also elsewhere on the board
MOTOR4: U$10.10; also elsewhere on the board
MOTOR5: U$10.11; also elsewhere on the board
MOTOR6: U$10.12; also elsewhere on the board
MOTOR7: U$10.5; also elsewhere on the board
MOTOR8: U$10.6; also elsewhere on the board
unnamed: U$11.1, U$12.1
NEUTRAL: U$10.2, U$11.2
RXD1: X1.1; also elsewhere on the board
RXD2: X2.1; also elsewhere on the board
RXD3: X3.1; also elsewhere on the board
SCK: X13.2; also elsewhere on the board
SENSOR1: JP2.1; also elsewhere on the board
SENSOR2: JP2.2; also elsewhere on the board
SENSOR3: JP2.3; also elsewhere on the board
SENSOR4: JP2.4; also elsewhere on the board
SENSOR5: JP2.5; also elsewhere on the board
SENSOR6: JP2.6; also elsewhere on the board
SENSOR7: JP2.7; also elsewhere on the board
SENSOR8: JP2.8; also elsewhere on the board
SS: X13.5; also elsewhere on the board
TXD1: X1.2; also elsewhere on the board
TXD2: X2.2; also elsewhere on the board
TXD3: X3.2; also elsewhere on the board

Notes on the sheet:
Connectors
Button Signals
Sensor Signals
Motors
Serial Pins
120 VAC Power
Cycle Sensors
+5V Out
Auxiliary Ports
Communication

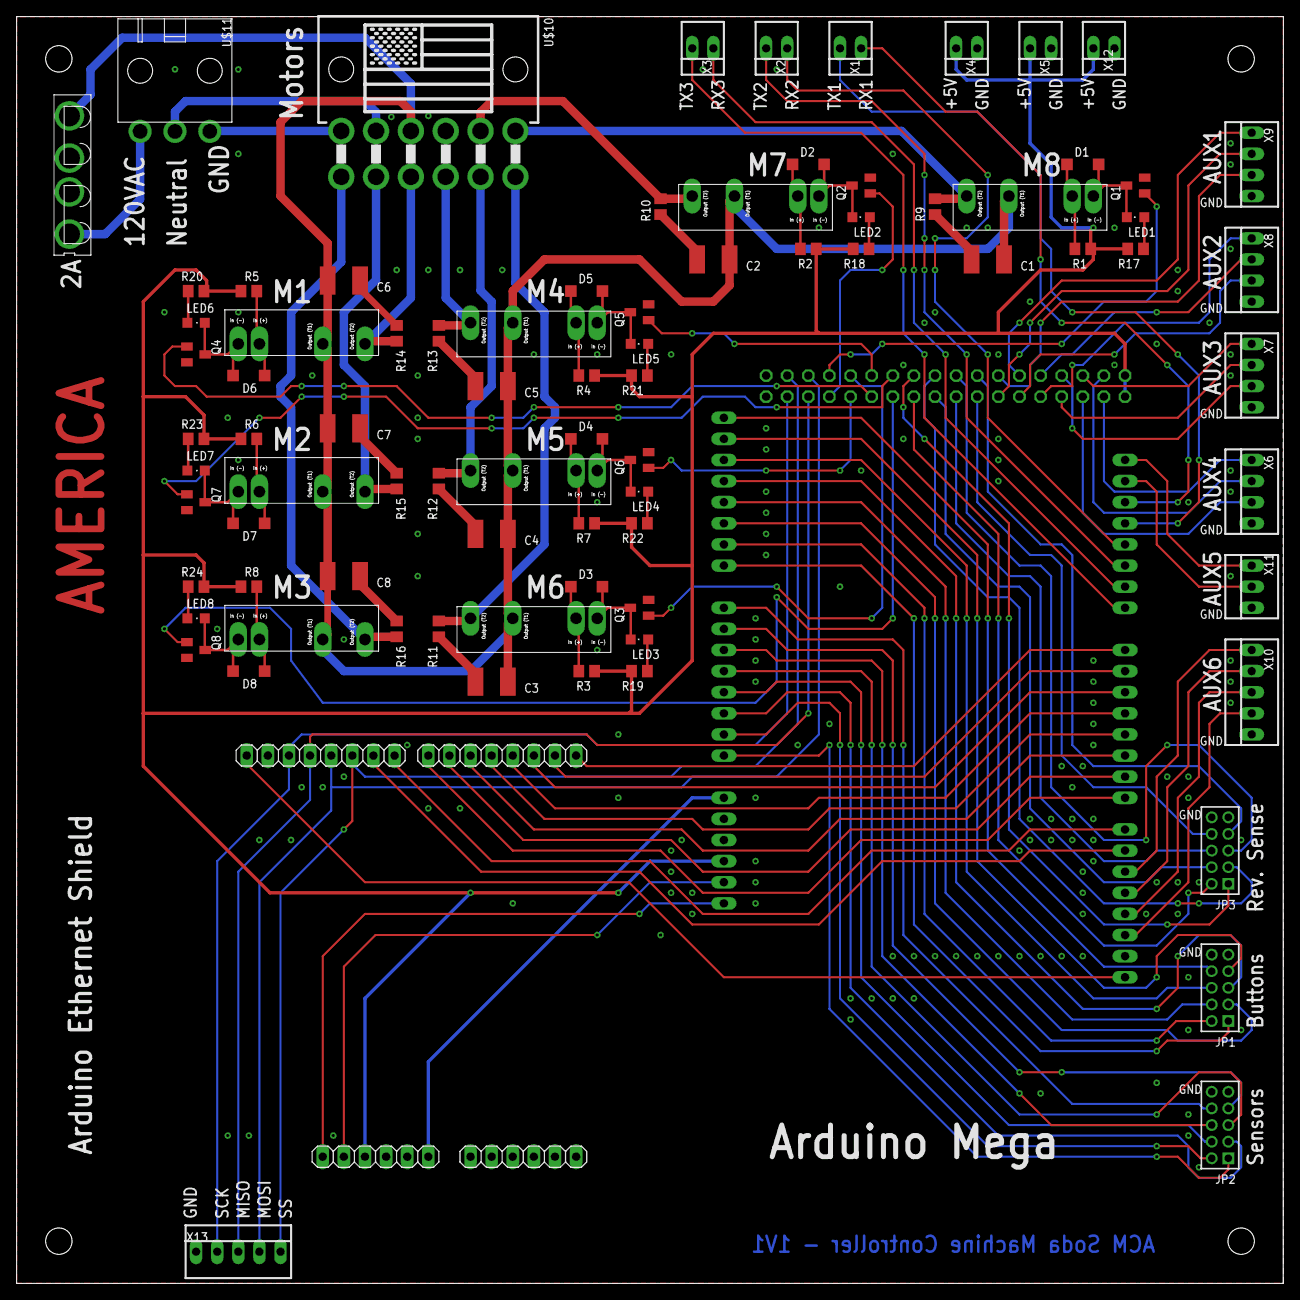
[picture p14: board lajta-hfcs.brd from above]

Board: 2 copper layers, 152.4 x 152.4 mm, 85 parts (1 on the bottom side), 120 nets.

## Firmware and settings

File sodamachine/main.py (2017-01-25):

#!/usr/bin/python
## Built-in modules
import os
import sys
import time
import pymysql
import serial
import settings
import log
from nanpy import ArduinoApi
from decimal import Decimal
from threading import Thread
##

## SodaMachine modules
# To import from the admin directory
from sodamachine.admin import *
# To import LCD object from the lcd module
from sodamachine.lcd import LCD
# To import Magstrip object from sodamag module
from sodamachine.magreader import MagStrip
##

def main():
    sysLog = log.createSystemLogger()
    ## Variables
    # Default account balance
    accountBalance = 0
    # Default char received data
    charReceived = ""
    # Cost of one soda
    sodaCost = .50 # 50 cents
    # Flow control variable for main program loop
    shouldContinueTrans = True
    ##

    ## Serial/USB connections
    # Initialize and connect to Arduino
    ser = serial.Serial(settings.SERIAL_PATH, 9600, timeout=10)

    # Initialize and connect to LCD
    lcd = LCD(0x0403, 0xc630)

    # Initialize and connect to Magstrip
    mag = MagStrip(settings.MAGSTRIP_PATH)
    ##
    
    try:
        ## Threaded processes
        # Start magstrip thread
        p = Thread(target=mag.read, args=())
        p.daemon = True
        p.start()
        sysLog.info('[SUCCESS] Magnetic Stripe thread successfully connected.')
        ##
    except:
        sysLog.error('[FAILURE] Failed to connect magnetic stripe thread.', exc_info=True)

    sysLog.info('[SUCCESS] Program initialization occured sucessfully.')

    # Main program loop
    while shouldContinueTrans:
        ####
        # @If: Integrity check to make sure the Serial port still active.
        #      If check fails, display error and attempt to reconnect
        #      every 10 seconds.
        # @Elif: Integrity check for LCD connection.
        #        If check fails, attempts to reconnect LCD once. Shuts down
        #        on failure.
        # @Else: Displays normal user time message on the LCD to show LCD working.
        ####
        if(not ser):
            try:
                ser = serial.Serial('/dev/arduino', 9600, timeout=10)
                lcd.write('Error Code: ARD\nContact Admin.')
            finally:
                time.sleep(10)
        elif(not lcd):
            try:
                lcd = LCD(0x0403, 0xc630)
            except:
                sys.exit("Unrecoverable LCD error.")
        else:
            # Display main message and current time
            ct = time.strftime("%I:%M %P")
            lcd.write('ACM Soda Machine\n    %s' % ct, 1)

        # Only process when card swiped
        if mag.studentID:
            sysLog.debug('Magnetic Stripe Reader read student ID: {0}'.format(mag.studentID))
            transactionHandler(ser, mag, lcd, sodaCost)
            # Reset IDs that were read
            mag.rawStudentID = ""
            mag.studentID = ""
            ser.reset_input_buffer()
            ser.reset_output_buffer()

def transactionHandler(ser, mag, lcd, sodaCost):
    transLogger = log.createTransactionLogger()
    ####
    # Creating a fresh transaction state for the user to ensure
    # no residual data is left over from previous transaction.
    ####
    ser.reset_input_buffer()
    ser.reset_output_buffer()

    ####
    # charReceived - stores the serial communication characters
    #                from raspberry pi
    # transFinished - Describes current transcation state
    ####
    charReceived = ""
    transFinished = False

    result = authorizeTransaction(mag, lcd)

    # If result is null then not valid user
    if not result:
        # Output invalid user to LCD
        lcd.write('No account found\nfor ID %s' % mag.studentID)
        transLogger.error('[FAIL] Failed to find account information for student ID: {0}'.format(mag.studentID))
    else:
        # Valid user
        transLogger.info('[SUCCESS] Sucessfully processed user {0} {1}'.format(str(result[3]),str(result[4])))
        transLogger.debug('Current Transaction results: {0}'.format(result))
        processTransaction(result, ser, mag, lcd, sodaCost, transLogger)

def authorizeTransaction(mag, lcd):
        lcd.write('Authorizing ...', 2)
        ####
        # Attempt to check for user
        ####
        try:
            result = checkUser.main(mag.studentID)
            return(result)
        except:
            print("[Error] Cannot check User in main.py.")
            return(False)

def processTransaction(result, ser, mag, lcd, sodaCost, logger):
    accountBalance = int(result[2]) # third record is account balance
    fname = str(result[3]) # fourth record is first name

    # Check accountBalance
    # Low balance
    if accountBalance < sodaCost:
        # Output low balance to LCD
        lcd.write('Sorry %s' % fname)
        lcd.write('Not enough funds\nfor transaction')

        errmsg = ('[NO FUNDS] the user {fname} {lname} currently has'
                  ' {curmoney} which is not enough for the soda price,'
                  '{price}').format(fname = fname, lname = str(result[4]),
                                    curmoney = accountBalance,
                                    price = sodaCost)
        logger.error(errmsg)
    # Sufficient Balance
    else:
        sucmsg = ('[HAS FUNDS] the user {fname} {lname} currently has'
                  ' {curmoney} which is enough for the soda price,'
                  '{price}').format(fname = fname, lname = str(result[4]),
                                    curmoney = accountBalance,
                                    price = sodaCost)

        logger.debug(sucmsg)
        # Output Make Selection to LCD
        lcd.write('Hello %s' % fname, 2)
        lcd.write('Please make\na selection', .1)
        try:
            # Send authorized to Arduino
            ser.write('a')
            logger.info('[SUCCESS] The \'a\' authorization character'
                         ' was succesfully written to the Arduino')
        except:
            logger.error('[FAILURE] The \'a\' authorization character'
                         ' failed to be written to the Arduino')

        finalizeTransaction(ser, mag, lcd, sodaCost, fname, accountBalance, logger)

def finalizeTransaction(ser, mag, lcd, sodaCost, fname, accountBalance, logger):
    ####
    # Start timeout clock if no serial transaction happens
    ####
    timeout = time.time() + settings.TIMEOUT_TIME
    transFinished = False
    logger.debug(('Timeout has been set to {0} and the Pi is waiting for'
                 'Arduino response.').format(timeout))

    while(not transFinished):
        charReceived = ser.read(1)
        if charReceived == 's':
            logger.info('[Success] Arduino has been succesful in dispensing'
                        ' soda')
            #####
            # If the transaction successfully completes, the
            # Arduino sends the index of the bottle they ordered
            # which corresponds with sloteData in settings.
            #####
            time.sleep(2)
            bottleOrdered = int(ser.read())
            while(not isinstance(bottleOrdered, int)):
               if(time.time() >= timeout):
                   print('BREAK')
                   break
               bottleOrdered = int(ser.read())

            print(bottleOrdered)
            logger.info(('[SUCCESS] {ID} has received the soda {soda}'
                         ' which has data of'
                         ' {data}').format(ID = mag.studentID,
                                           soda = settings.slotData[bottleOrdered]["name"],
                                           data = settings.slotData[bottleOrdered]))
            # Deduct sodaCost from amount
            # NOTE: change for modular prices
            changeAmount.main(mag.studentID, -sodaCost)
            logger.debug('{ID} has been charged {cost}'.format(ID = mag.studentID,
                                                               cost = sodaCost))
            # Output success & new balance to LCD
            lcd.write('Thank you, %s' % fname)
            ###
            # Normalizing account balance for user
            ###
            accountBalance = ((Decimal(accountBalance))/100-Decimal(.5))
            lcd.write('Remaining\nBalance: ${0:.2f}'.format(accountBalance)) #Temporary
            logger.debug(('{ID} has a remaning balance of'
                          ' {bal}').format(ID = mag.studentID,
                                           bal = accountBalance))

            transFinished = True


        # Vending error from Arduino
        elif charReceived == 'e':
            # Output error to LCD
            logger.error('There was an error dispensing the Soda')
            lcd.write('Error dispensing\nPlease try again')
            transFinished = True
        elif charReceived == 'o':
            # Output error to LCD
            lcd.write('Out of Stock.')
            logger.error('The soda machine is out of stock of the soda'
                         ' the user ordered.')
            transFinished = True
        # Took too long to make a selection
        elif(time.time() >= timeout):
            logger.info('The transaction timed out.')
            ser.write("t")
            lcd.write('Transaction\ntimed out')
            transFinished = True


if __name__ == "__main__":
    # Call main function
    main()

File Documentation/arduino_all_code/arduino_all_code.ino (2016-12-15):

/*************************************************/
/*      ACM Soda Machine Dispensery Systems      */
/*      Written by - Nic Pereira                 */
/*      Circuitry by - Nathan Szanto             */
/*      Arduino uses a C based language,         */
/*       other documentation can be found here:  */
/*       http://arduino.cc/en/Reference/HomePage */
/*************************************************/

//NOTES OF CODE:
//1. Current code does not support sodas having different prices.

//motor switches for dispense duration
//buttons for dispense
//motor switches for lights
//card swipe for money

const int Button[8] = {A8, A9, A10, A11, A12, A13, A14, A15};
const int Motor[8] =  {44, 43, 42, 45, 46, 47, 48, 49};
const int MotorSw[8] = {41, 40, 39, 38, 37, 36, 35, 34};
const int StockSw[8] = {A0, A1, A2, A3, A4, A5, A6, A7};
const int TIME = 2*(1000);

void serialFlush()
{
  while(Serial.available())
  {
    int clearBuffer = Serial.read();
    delay(1);
  }
  Serial.flush();
}

void setup()
{
  /////
  // Settings up the defaults for the Pi.
  // Buttons, Stock Switches, and Motor Switches must be set to INPUT_PULLUP
  // for proper interaction, see look online for INPUT_PULLUP documentation
  // for more information..
  /////
  Serial.begin(9600);
  serialFlush();
  for(int i = 0; i< 8; i++)
  {
    pinMode(Button[i], INPUT_PULLUP);
    pinMode(StockSw[i], INPUT_PULLUP);
    pinMode(MotorSw[i], INPUT_PULLUP);
  }
}

void loop()
{
  bool transFinished = false;
  if(Serial.available())
  {
    /////
    // Read the character sent by the Raspberry Pi to the Arduino to see the
    // state of the transacation
    /////
    char valLetter = (char)Serial.read();
    if(valLetter == 'a')
    {
      while(!transFinished)
      {
        /////
        // Cycles through all of the buttons on the panel and checks if any
        // of them are pressed
        /////
        for(int i = 0; i< 8;)
        {
          //////
          // Checks to make sure that the transacation has not timed output
          //////
          if(!Serial.available())
          {
            if(digitalRead(Button[i]) == LOW)
            {
              /////
              // Checks to see if the soda the user selets is still in stock
              /////
              if(digitalRead(StockSw[i]) == HIGH)
              {
                /////
                // Regulating the motor to properly dispense the soda.
                // (I.E. it turns until it fully completes a revolution).
                /////
                digitalWrite(Motor[i], HIGH);
                delay(TIME);
                while(digitalRead(MotorSw[i]) == LOW);
                digitalWrite(Motor[i], LOW);

                /////
                // Write the the Pi that the transaction was successful
                /////
                Serial.write("s");
                /////
                // Write to the Pi which soda that the user ordered and finish
                // transaction.
                /////
                Serial.print(i);
                transFinished = true;
                break;
              }
              else
              {
                //////
                // Writes to the Pi that the soda is out of stock and ends
                // transaction.
                /////
                Serial.write('o');
                transFinished = true;
                break;
              }
            }
            else
            {
              /////
              // Manually progressing the For loop for better control
              /////
              i++;
            }
          }
          else
          {
            /////
            // Checks to see if it reads the Timeout character from the
            // Pi. If so, it ends the transaction
            /////
            if((char)Serial.read() == 't')
            {
              transFinished = true;
              break;
            }
          }
        }
      }
    }
    else
    {
      Serial.write("e"); //Signals that transaction failed
    }
  }
  /////
  // Resets the transaction state.
  /////
  serialFlush();
}

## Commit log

2016-12-15 [ADD] Fix addUser implementation and Plug-And-Play
    [main.py]
2017-01-25 [UPDATE] Python Requirements + Minor Fixes
    [main.py]
